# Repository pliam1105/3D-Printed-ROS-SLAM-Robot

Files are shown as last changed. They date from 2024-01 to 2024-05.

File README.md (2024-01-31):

# 3D Printed ROS SLAM Robot
A **3D printed robot** that runs on the **Robot Operating System (ROS 2)** and uses a LiDAR to autonomously navigate around and map a room (**Simultaneous Localization And Mapping**).

https://github.com/pliam1105/3D-Printed-ROS-SLAM-Robot/assets/34167782/ba77c825-f32c-44ad-a219-17dad1da1876

The idea for the project was inspired by James Bruton's [ROS SLAM robot](https://www.youtube.com/watch?v=q1u_cC-5Sac), hence the similarity in some parts of the chassis design and electronics (but everything was designed and built from scratch).

## 3D Printed Chassis

For the chassis I decided to learn about CAD design and 3D printing and make it from scratch. Therefore, I learned how to use **Fusion 360** and designed the required components part-by-part, starting with the motor mounts, next the gears and wheels connected with the drive part, and then connecting them and adding the top platform for the LiDAR and electronics.

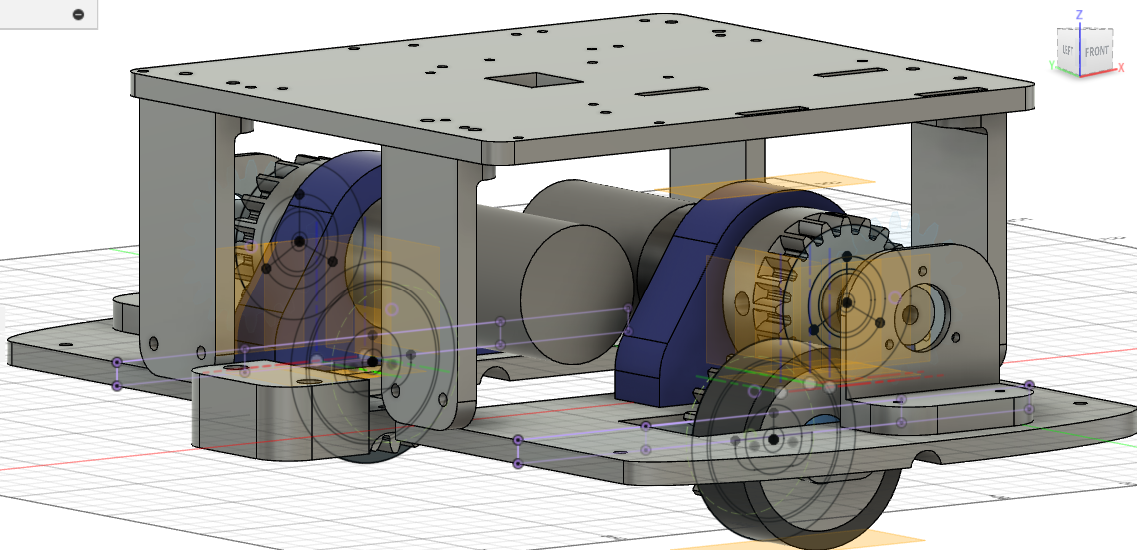
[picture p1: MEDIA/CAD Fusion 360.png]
<table><tr><td align="center"></td></tr><table>

Then I **3D printed** all the parts in my Ender 3 and assembled them with 2 aluminum extrusions, various screws, a rod connecting the wheels, and a couple of ball casters. I also installed all the electronics listed in the next section.

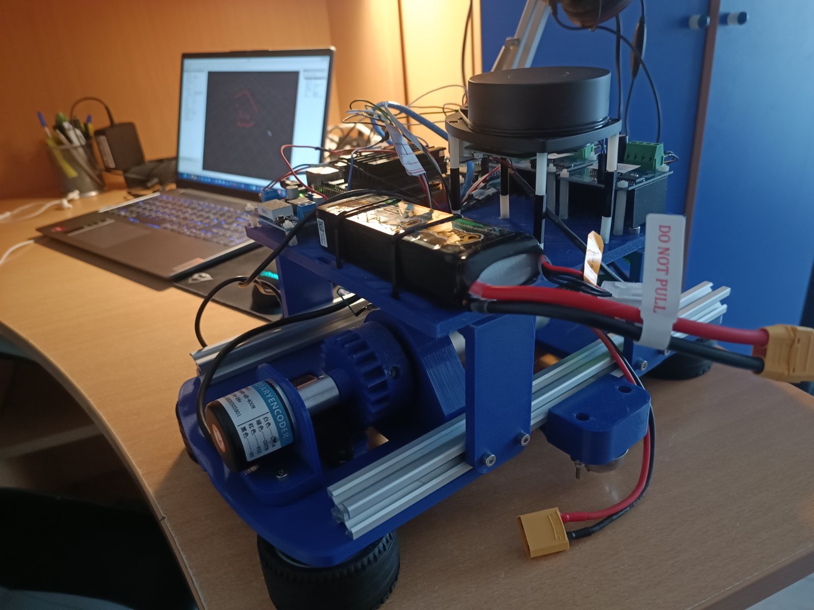
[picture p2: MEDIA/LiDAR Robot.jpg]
<table><tr><td align="center"></td></tr><table>

## Hardware & Connections

The electronics components that I used are the following:

* Two **planetary gear 12V DC motors** (gear ratio $19.2:1$) and two **BTS7960 motor drivers** to control them with the Arduino.
* Two **incremental rotary encoders** for odometry data and controlling the motor speed
* An **RPLiDAR A1** for gathering distance measurements in a $360\degree$ range around the robot
* An **Arduino Mega 2560** to control the motors and record the encoder measurements
* An **NVIDIA Jetson Nano**, working on Ubuntu 20.04 and having ROS 2 Foxy installed, to manage the nodes communicating with the Arduino via Serial for motor control and odometry data transmission

To power the robot, I use:

* A **12V 3S Li-PO battery** that directly powers the motors
* An **LM2596 adjustable step down module**, set to 5V to power the encoders
* A **power bank** (or battery charger) for the Jetson Nano
* The Arduino is powered directly via USB (which also works as Serial) by the Jetson Nano

The connections between the components are depicted in the below Fritzing diagram.

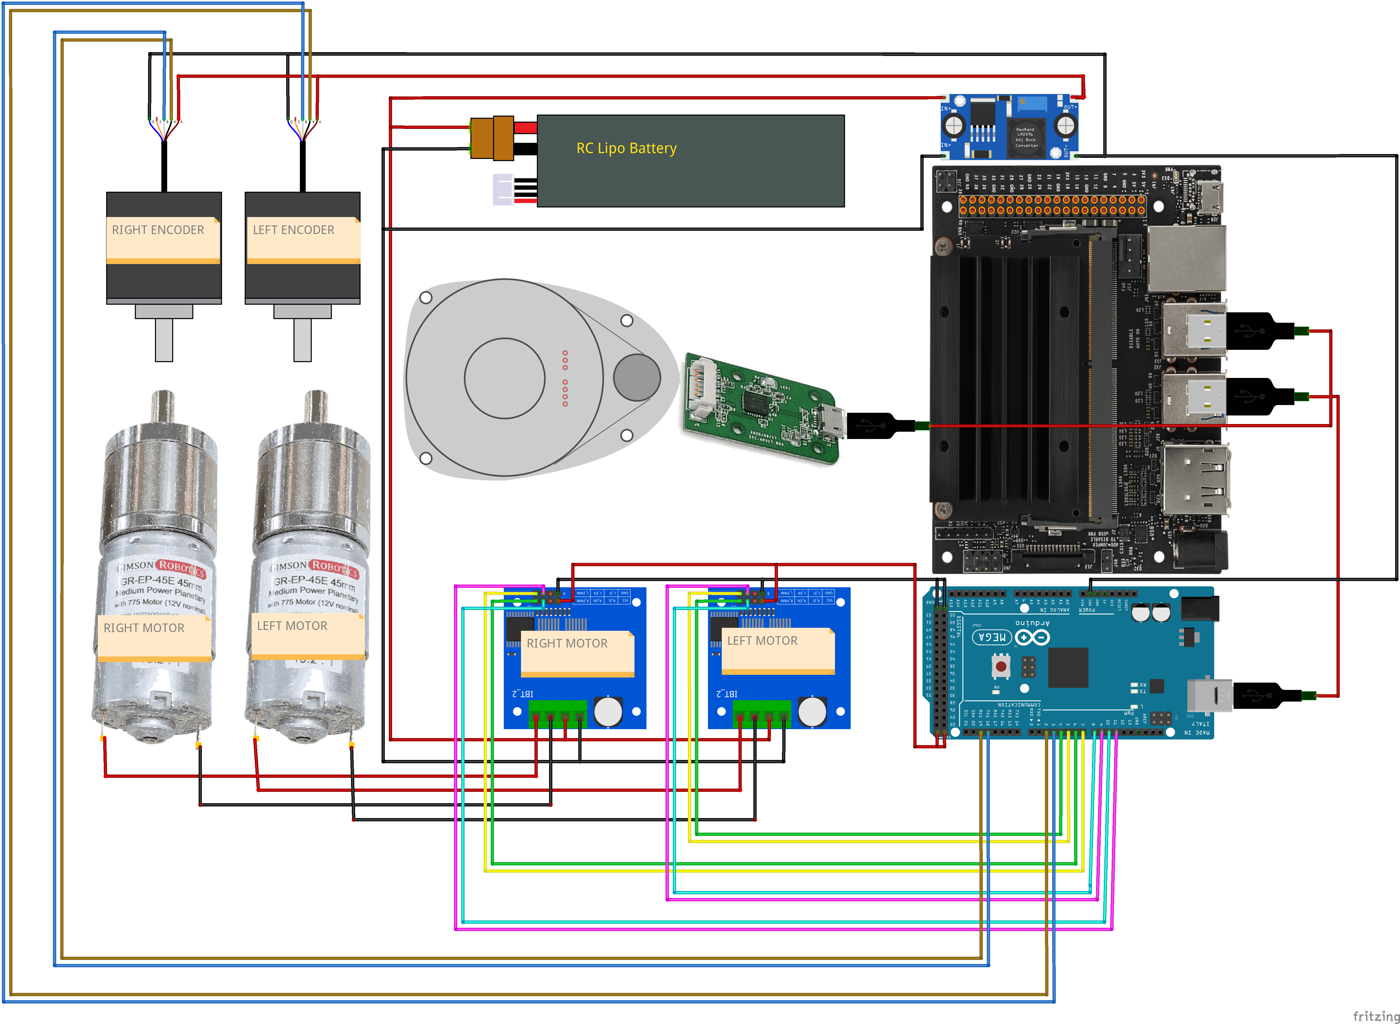
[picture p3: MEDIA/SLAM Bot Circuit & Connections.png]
<table><tr><td align="center"></td></tr><table>

## Arduino Motor Control with PID ([code](Arduino%20Codes/ROSSerial/ROSSerial.ino))

In order to control the motors, I used an Arduino that transfers the velocity commands (given as linear and angular velocity components) from the Jetson Nano and returns the wheels' speeds at any moment.

### Encoder speed calculation and conversion to $m/s$

The first thing needed was to **measure the encoders' rotation speed and direction**. The encoders have two pins, A and B, which give a `HIGH` or `LOW` signal with a phase difference of $90\degree$. Therefore, to measure the speed of rotation we attach an **interrupt** at pin A that triggers when its signal *rises* from `LOW` to `HIGH` (pulse), and count the number of pulses at a certain time interval. To detect the direction we check if the value of B signal is the same as A when we detect a pulse.

Then, to get the speed in terms of $m/s$ (as required by ROS) instead of $pulses/millisecond$ as computed before, I needed to measure the amount of pulses that account to a meter of robot displacement. To do that I put a measuring tape on the ground, moved the robot 1 meter, and noted the number of pulses on the encoders (although later it turned out to not be accurate so I ran the PID controller described below on a certain speed for a specific time and calculated the conversion rate again based on the distance covered).

<table>
    <tr>
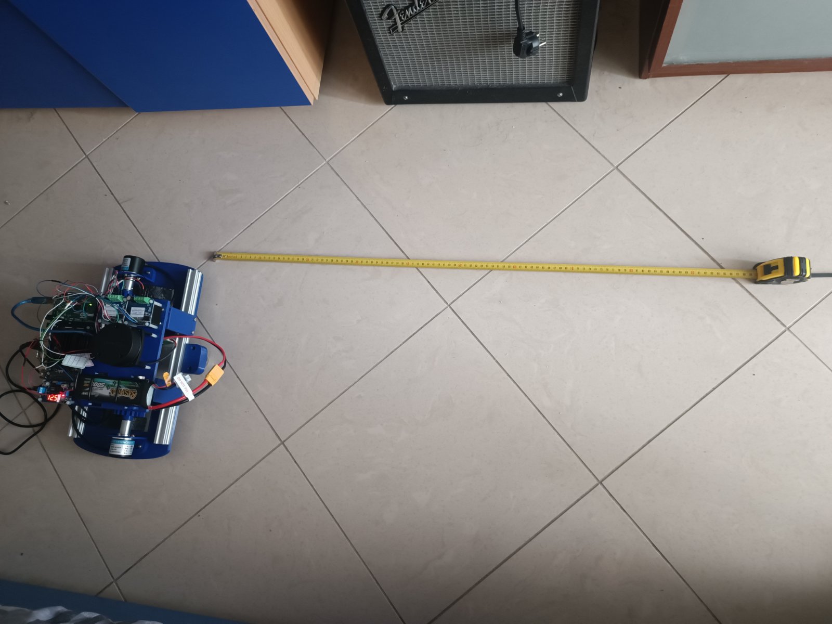
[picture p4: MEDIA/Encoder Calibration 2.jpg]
        <td align="center"></td>
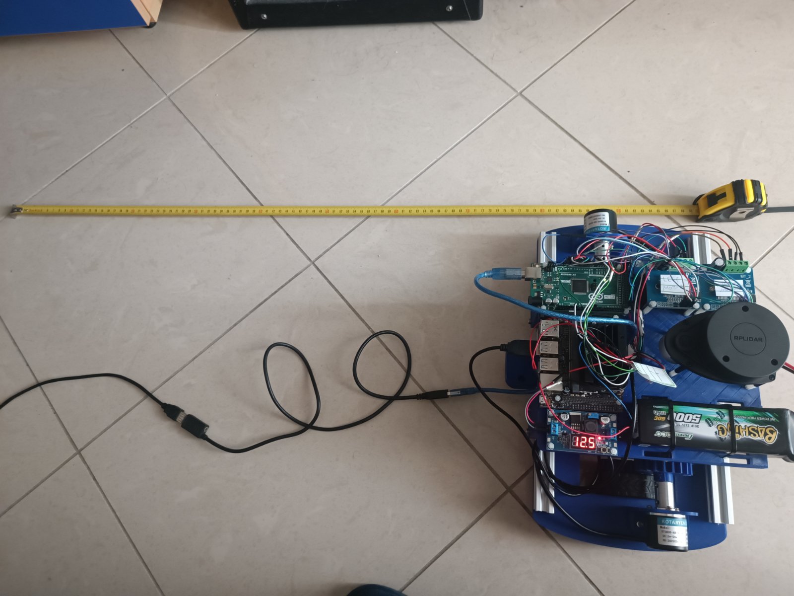
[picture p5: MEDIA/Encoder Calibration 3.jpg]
        <td align="center"></td>
    </tr>
<table>

### PID controller and differential drive

The next, and most important, thing to be implemented is being able to convert the $(linear, angular)$ velocity commands from ROS to **motor speeds**, and **apply them to the motors**, in order to move the robot in the intended way. We first need to convert the 2 given velocity components to the wheel speeds (in $m/s$), that is, implement **differential drive**, which is done using the formulae:

$$
left\ wheel\ speed = linear_X - angular_Z \cdot wheel\ separation / 2
$$

$$
right\ wheel\ speed = linear_X + angular_Z \cdot wheel\ separation / 2
$$

To make the motors move in those specific speeds and mitigate the effects of different motor powers, asymmetrical forces, slippage, and various others, we use a **PID Controller**, which is a *closed loop controller* that gets the encoder measured speeds (*input*) and changes the motors' PWM duty cycle (*output*), using the motor drivers, with the goal of achieving certain speeds. I used the `PID_v1` Arduino library, and tuned the $KP$, $KI$, $KD$ parameters via trial-and-error, finally achieving fast convergence to the intended speed with great accuracy.

## ROS Motor Control Node ([code](ROS%20Codes/arduino_serial/))

Then, I needed to get ROS working with the Arduino and be able to send velocity commands via the `cmd_vel` topic, and receive odometry data via the `odom` one, also publishing the transform `odom` $\rightarrow$ `base_link` (the position and orientation of the robot estimated by the encoder measurements), for which I will explain more in the [SLAM](#slam-node) section.

On the Jetson Nano side, I installed ROS 2 Foxy, working with Ubuntu 20.04, and implemented a package from scratch (`arduino_serial`) that contains the node (with the same name) that will undertake the above functionality.

### Arduino - Jetson Nano Serial Communication

The only feasible way to transmit the required data from/to the Arduino, since the `rosserial` library only works on ROS 1 and `micro-ROS` doesn't work on older Arduino boards, was to use serial communication between Jetson Nano and Arduino. To that end, I used the [`SerialTransfer`](https://github.com/PowerBroker2/SerialTransfer) library and its Python counterpart, [`pySerialTransfer`](https://github.com/PowerBroker2/pySerialTransfer), to send and receive packets of data.

At any moment, I wanted to send velocity commands in the form described [above](#pid-controller-and-differential-drive), but also receive the speed of each wheel, measured by the encoders. That required synchronized data transfer between Jetson Nano and Arduino. When initializing the ROS node and in the Arduino `setup()` function, I made a *handshake* between those two, that is, send a request every 1 second from the Jetson Nano and wait until Arduino responds. Then, at every cycle of the ROS node and the Arduino (which usually have phase difference):
* In the Jetson Nano side, I first send the velocity commands, then wait to receive the encoder speeds from the Arduino
* In the Arduino side, I first wait to receive the velocity commands, then send the encoder speeds

To do that, I needed to send data even when there weren't any new commands or encoder speeds, so I just resent the latest values available.

### Velocity Commands

As mentioned above, the `arduino_serial` node subscribes to the `/cmd_vel` topic to get messages of type `Twist` ,containing $angular\ x,y,z$ and $linear\ x,y,z$ components, from which we only care about the $linear_x$ and $angular_z$ ones, which it then forwards to the Arduino. I tested that functionality using the `teleop_twist_keyboard` package and the respective node.

### Odometry feedback and pose estimation

The navigation nodes used in the [next section](#simultaneous-localization-and-mapping-code) require the publishing of `Odometry` messages, containing the estimated pose and velocity of the robot, as well as the transform `odom` $\rightarrow$ `base_link`, that is, the estimated pose frame (`base_link`) with respect to a fixed frame (`odom`).

I compute the $(linear, angular)$ velocity components using the following formulae:

$$
linear_x = (left\ wheel\ speed + right\ wheel\ speed) / 2
$$

$$
angular_z = \frac{right\ wheel\ speed - left\ wheel\ speed}{wheel\ separation}
$$

I also time-integrate the wheel speeds to get the pose estimation using the following formulae (applied at each time-step with new encoder data):

$$
\text{Angle displacement:}\ d\theta = angular_z \cdot dt
$$

$$
\text{Distance left wheel traveled:}\ d_{left} = left\ wheel\ speed \cdot dt
$$

$$
\text{Distance right wheel traveled:}\ d_{right} = right\ wheel\ speed \cdot dt
$$

$$
\text{Distance point of reference (center) traveled:}\ d_{center} = (d_{left} + d_{right})/2
$$

$$
\text{$x$ displacement:}\ d_x = d_{center} \cdot \cos{(\theta + d\theta/2)}
$$

$$
\text{$y$ displacement:}\ d_y = d_{center} \cdot \sin{(\theta + d\theta/2)}
$$

$$
\text{New $x$ coordinate:}\ x' = x + dx
$$

$$
\text{New $y$ coordinate:}\ y' = y + dy
$$

$$
\text{New $\theta$ orientation:}\ \theta' = \theta + d\theta
$$

I tested the odometry pose estimation by moving the robot around with `teleop_twist_keyboard` around the room and checking the drift of LiDAR data with respect to a fixed coordinate frame (`odom`), by visualizing it with RViz 2.

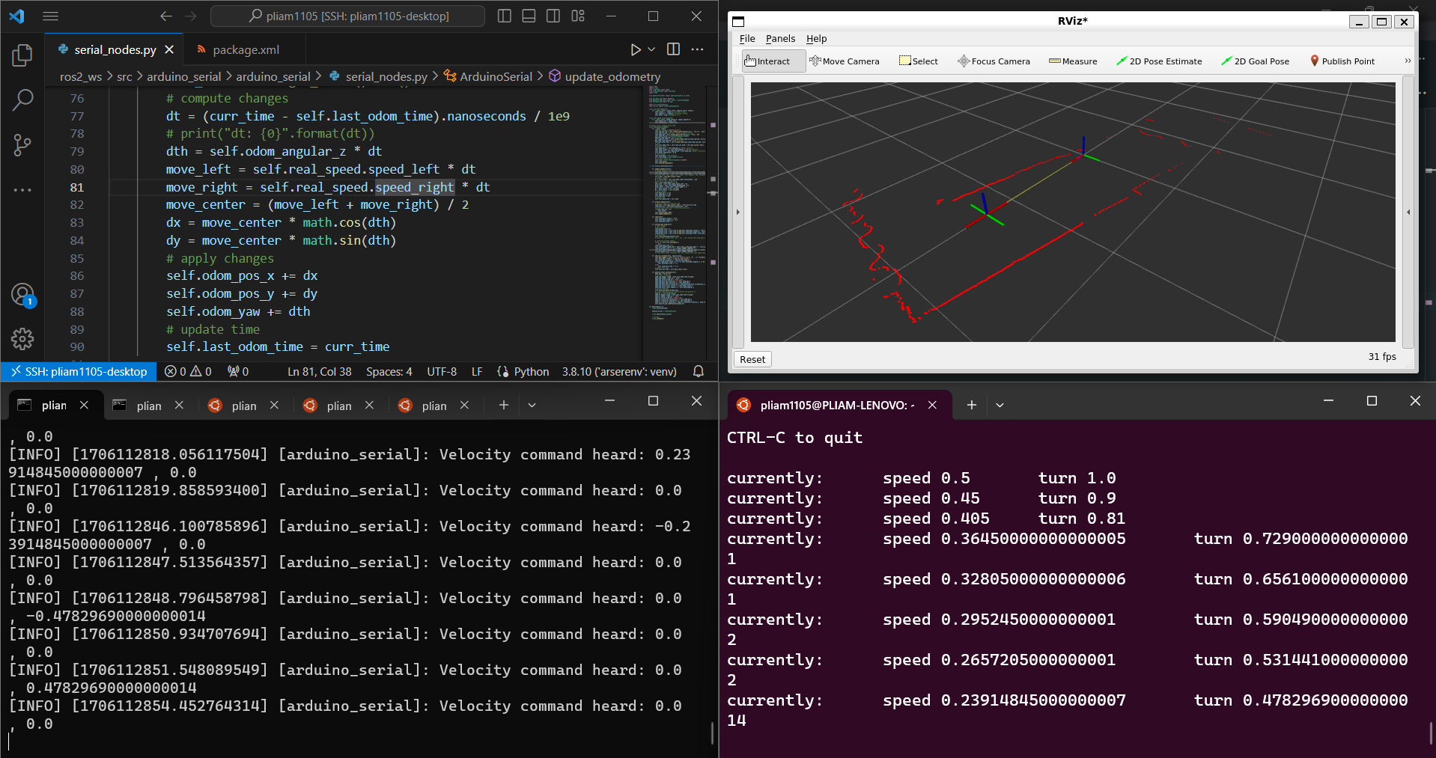
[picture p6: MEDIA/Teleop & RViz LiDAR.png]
<table><tr><td align="center"></td></tr><table><br>

## Simultaneous Localization and Mapping ([code](ROS%20Codes/slam_bot/))

The next step, after being able to control the robot's velocity and get a pose estimation based on its encoders, is to incorporate LiDAR data and implement **Simultaneous Localization and Mapping (SLAM)**, and also **navigate** around the room autonomously.

### LiDAR Node

To convert the LiDAR data, which are transmitted via USB to the Jetson Nano, to a ROS-compatible format (`LaserScan` messages), I used the [RPLiDAR ROS](https://github.com/allenh1/rplidar_ros) library, which launches a node that publishes to the `/scan` topic, which I could visualize in RViz 2 as shown below.

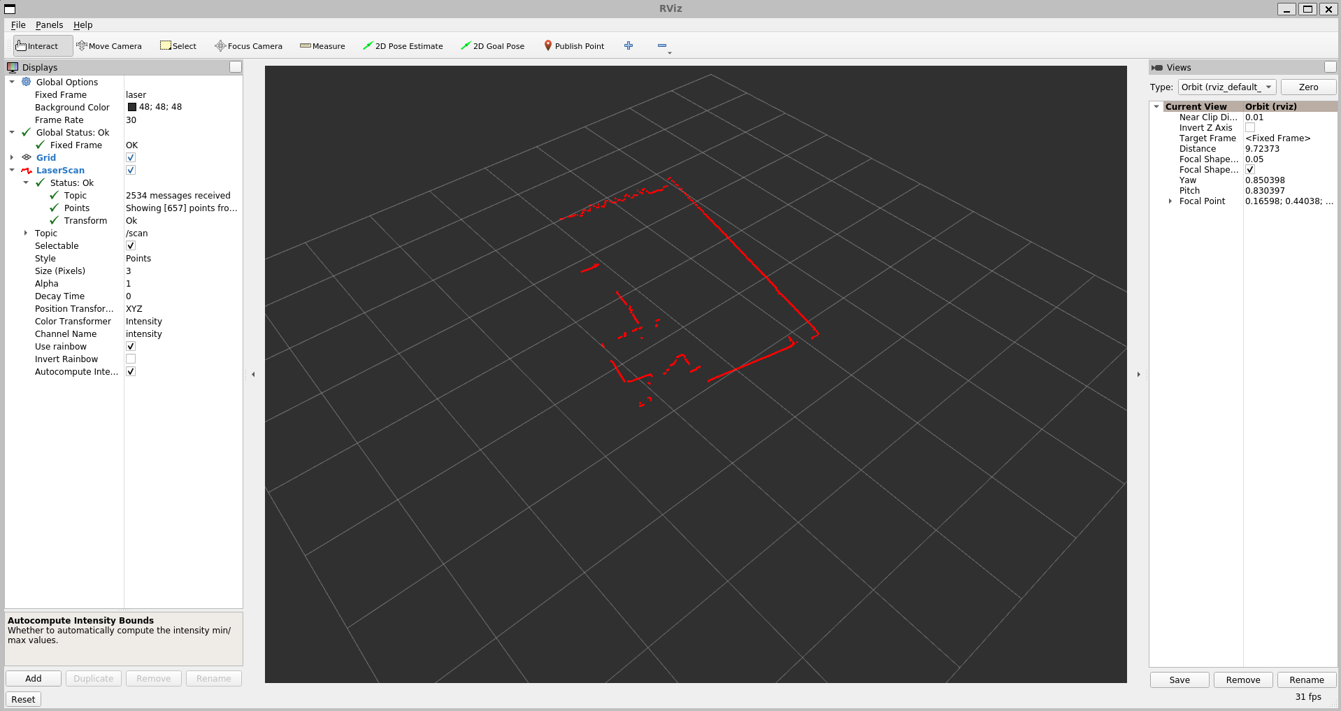
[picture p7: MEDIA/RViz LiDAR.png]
<table><tr><td align="center"></td></tr><table><br>

### Robot & Joint State Publishers

ROS coordinates are based on certain *frames*, that is coordinate frames that are related with each other using *transforms* (which can be published and computed using `tf2`), that are all part of the *TF tree*. In terms of the robot, these frames are described using *links*, which are connected with each other via child-parent relationships and defined using translations.

Therefore, a robot is described by defining all these links and relations in a URDF file (an XML file). This description is published in the TF tree using a *Robot State Publisher* (using the `robot_state_publisher` package and respective node).

Also, since there are joints with variable orientation (or other types of movement), their states are published using a *Joint State Publisher* (using the `joint_state_publisher` package and node and their GUI counterparts that enable changing the states using sliders).

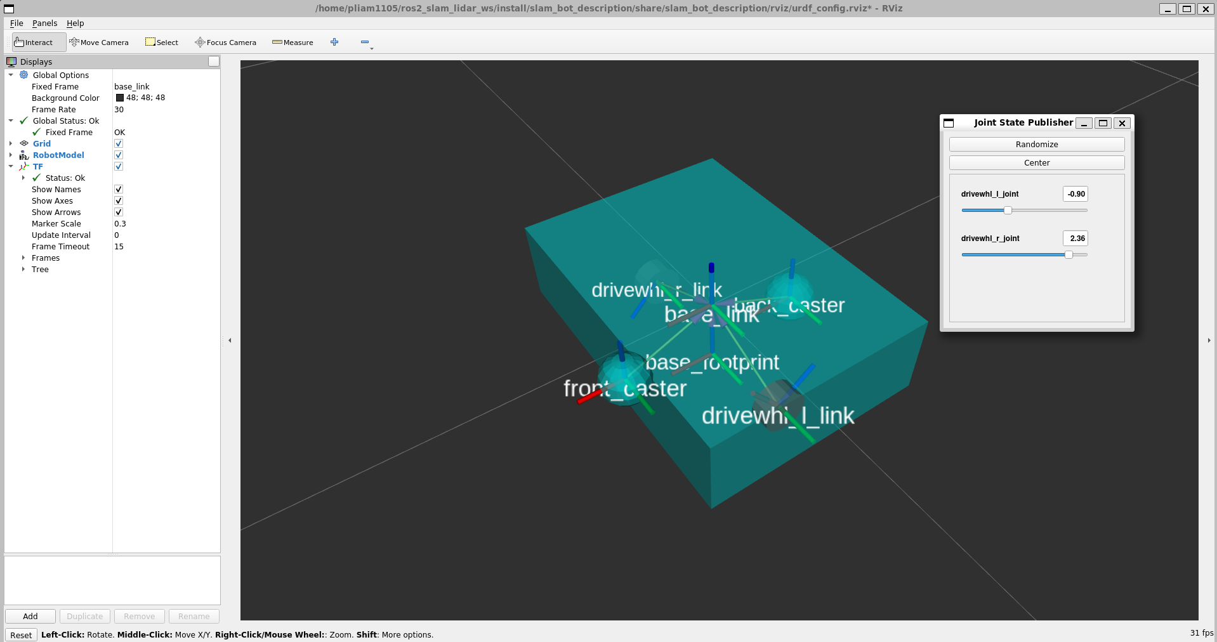
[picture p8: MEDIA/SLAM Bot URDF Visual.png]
<table><tr><td align="center"></td></tr><table><br>

### SLAM Node

This is the point where all the above aspects start connecting with each other. The fundamental part of an autonomous robot is being able to **map an unknown area and localize itself in it**; this is the essence of **SLAM**. To implement that functionality, I used the `slam_toolbox` package, specifically the `async_slam_toolbox_node` node, which receives the odometry and sensory data published and creates a map, which it aligns with the robot's coordinate frame to predict a more accurate location estimation.

That's where the coordinate transforms mentioned in the [Motor Control Node](#ros-motor-control-node-code) section come handy. The core frames used in localization and mapping using ROS are: `map`, `odom`, and `base_link` (and `base_laser` or `laser` representing LiDAR, but this is usually computed with respect to `base_link`).

* `map` is the frame that represented the real-world environment of the robot, which is supposed to be stationary
* `odom` is the frame that stays fixed with respect to the starting position of the robot, and is used to depict the robot's odometry location estimate
* `base_link` is the frame that represents the robot's position

The `odom` $\rightarrow$ `base_link` transform is computed as described in the [odometry](#odometry-feedback-and-pose-estimation) section, using the encoder data.

The `map` $\rightarrow$ `odom` transform is computed by the localization node, in this case one from the `slam_toolbox` package, and its purpose is to align the robot's estimate of its position with the map of its environment using its sensory data.

The result of that functionality is visualized as shown below, in RViz 2.

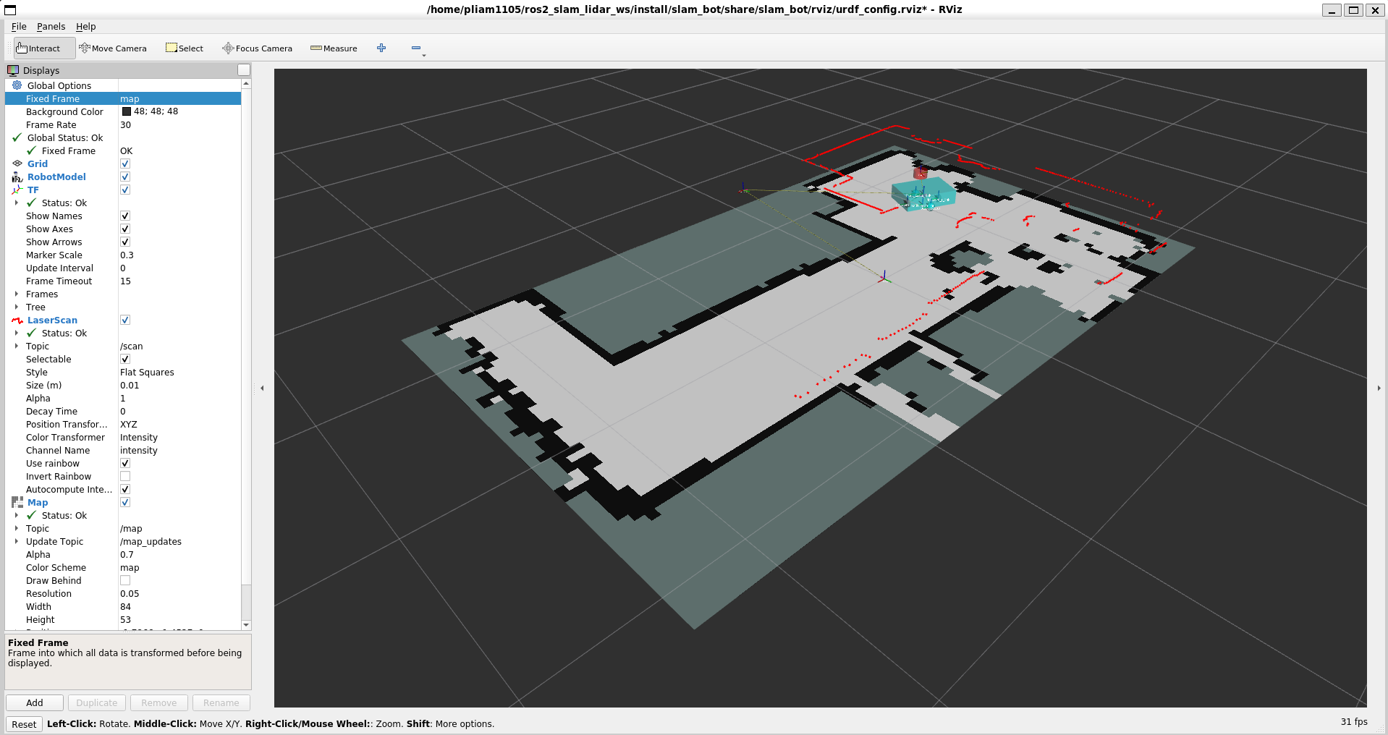
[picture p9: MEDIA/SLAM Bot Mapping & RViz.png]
<table><tr><td align="center"></td></tr><table><br>

### Navigation Nodes

After locating itself in the environment, the robot's purpose is to complete tasks in it, and this involves moving to specific locations on its own. This is the navigation part of the project, which is implemented using the `navigation2` package (and the `nav2_bringup` to launch all the required nodes at once).

It takes the map computed from `slam_toolbox` and creates a *costmap* based on it, that is, a map representing the ability to traverse each part of the map, with relation to the occupied areas (which are also *inflated* by a radius, accounting for the robot's size).

Then, a *planner* takes that costmap and the end goal given by the user (via RViz or a service call), and computes, for some time ahead, the optimal path to achieve that goal. This updates at specific intervals, taking into account the new state of the robot and updated map.

Finally, a *controller* takes the path computed by the planner and publishes the velocity commands to follow it, which then the Arduino receives and applies motor speeds accordingly. The controller also updates at specific intervals, integrating the newest path and robot state received.

There are also some *backup nodes* that are activated in certain instances to recover the robot's location and find a new way to accomplish the goal (all this structure works using decision trees).

A visualization of the state of the robot, the map, and the path computed in a certain instance, in RViz 2 is provided below.

<table><tr><td align="center"><img src="MEDIA/SLAM Bot Navigation RViz.jpg" width=75%"></td></tr><table><br>

## Final Result

The final result is a robot that is able to **receive end goal commands and navigate to them on its own**, able to adapt to unknown environments and unexpected instances effectively. A snippet of the robot working in real life is given below.

<table><tr><td align="center"></td></tr><table><br>

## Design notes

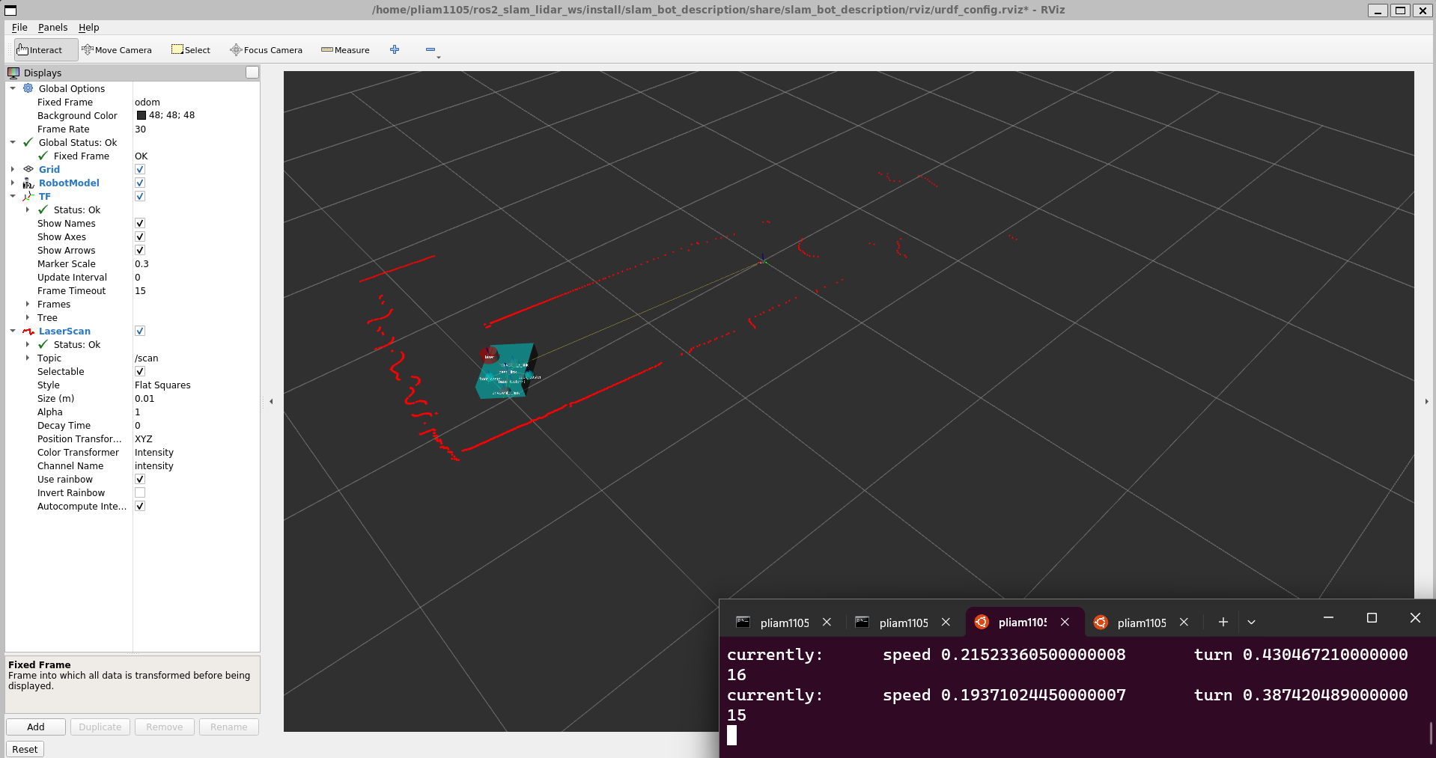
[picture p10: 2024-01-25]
MEDIA/Teleop LiDAR & Odom RViz URDF.png

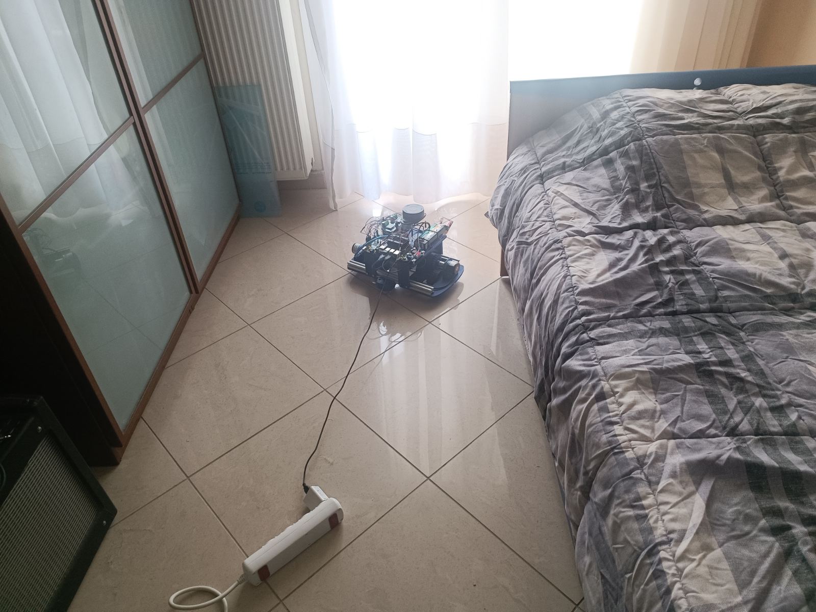
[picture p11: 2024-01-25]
MEDIA/LiDAR URDF Odom RViz Room Image.jpg

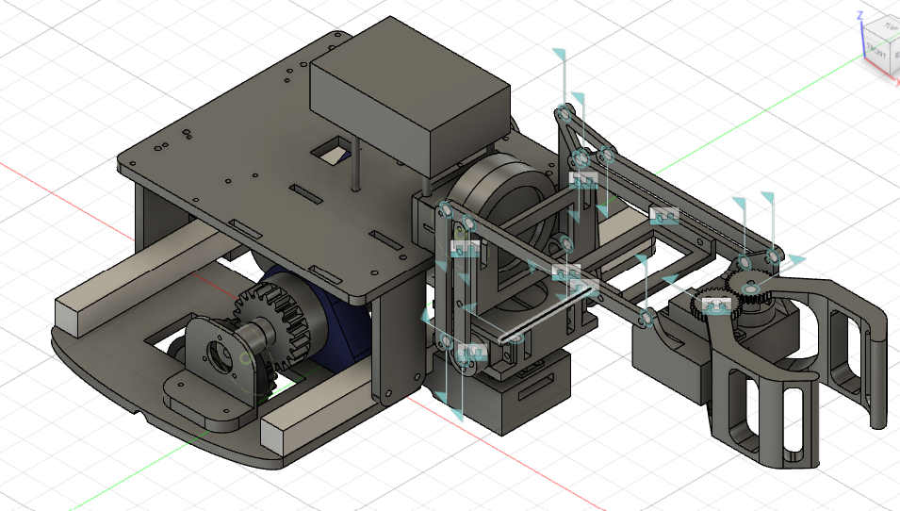
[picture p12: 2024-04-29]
MEDIA/SLAM Bot CAD with Robotic Arm and Camera.png

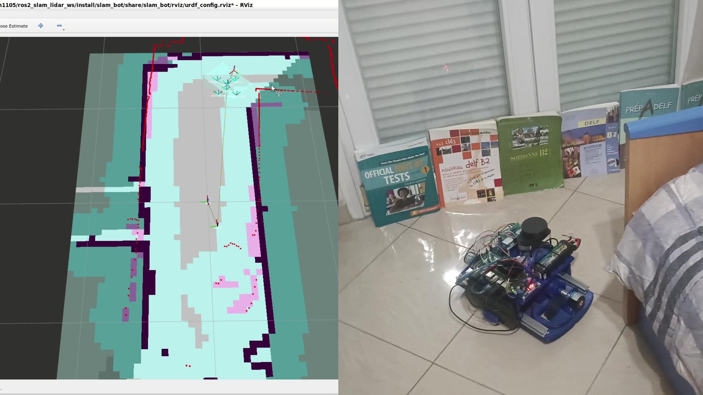
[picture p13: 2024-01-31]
MEDIA/SLAM Navigation RViz & Camera Image.jpg

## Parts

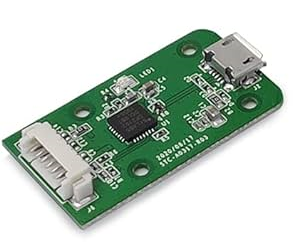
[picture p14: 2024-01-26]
Fritzing Connections/Parts/RPLiDAR USB Connector.png

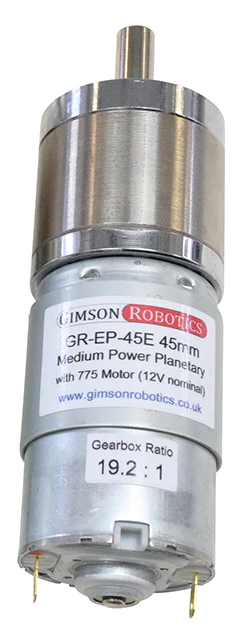
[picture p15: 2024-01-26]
Fritzing Connections/Parts/Planetary Gearmotor.png

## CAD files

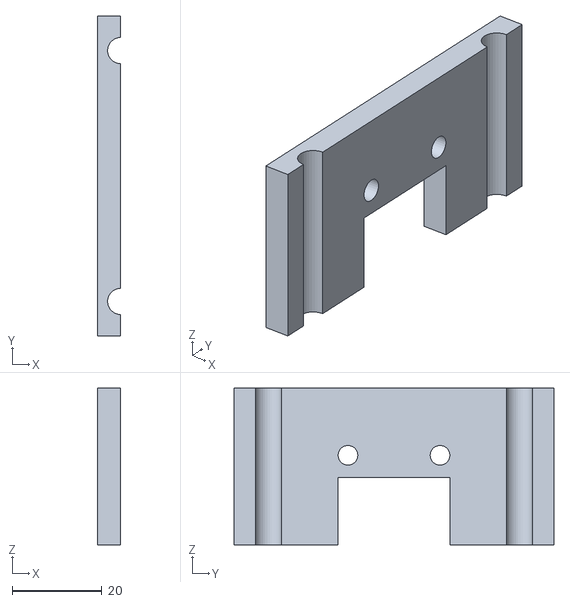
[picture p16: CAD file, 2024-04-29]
3D PRINT/STL/Camera Mount/SpacerMountBack.stl
5.22 x 71.5 x 35.0

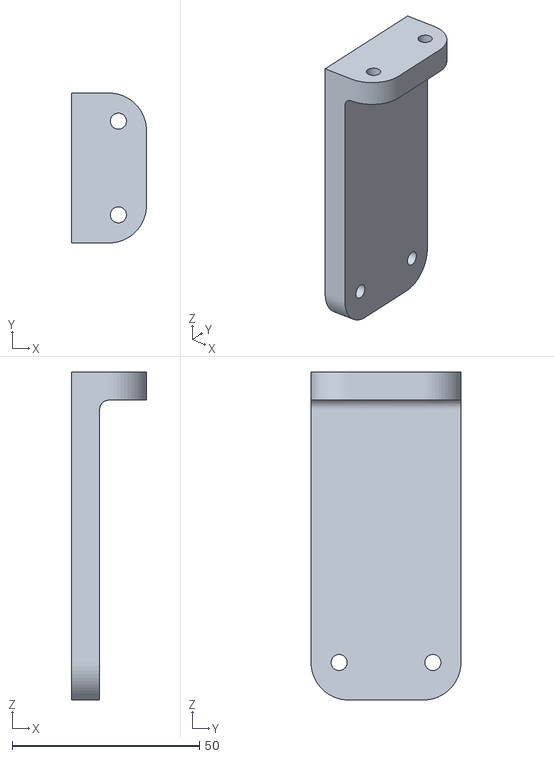
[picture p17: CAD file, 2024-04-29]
3D PRINT/STL/Connector.stl
20.0 x 40.0 x 87.5

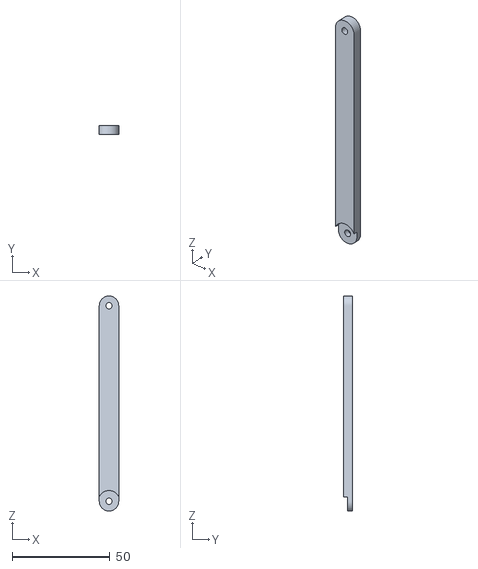
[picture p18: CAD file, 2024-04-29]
3D PRINT/STL/Robotic Arm/RightParallelLink.stl
10.0 x 4.50 x 110.0

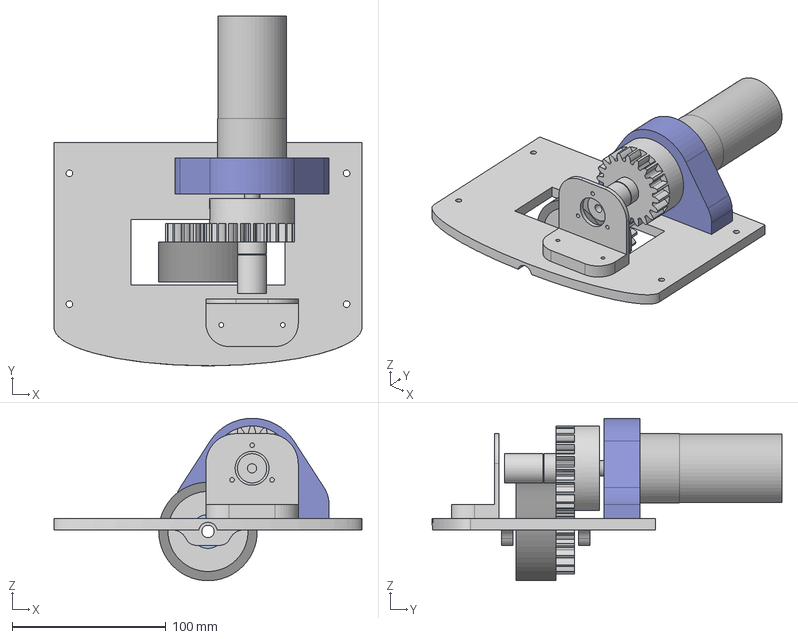
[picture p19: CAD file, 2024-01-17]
Fusion360/Drive.step
200.0 x 227.0 x 105.5 mm
Spur Gear (20 teeth)
Motor
Spur Gear (20 teeth) (1)

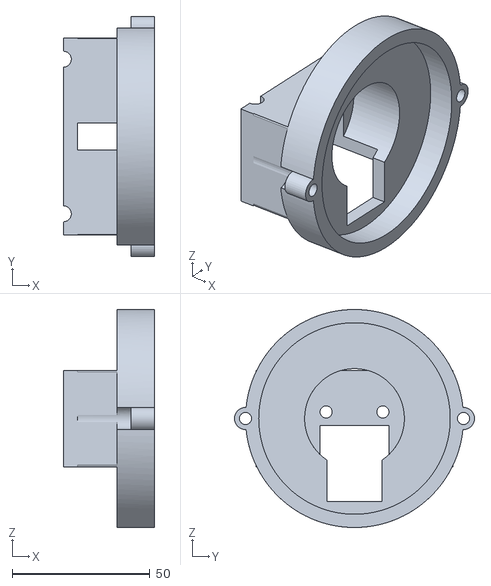
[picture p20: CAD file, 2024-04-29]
3D PRINT/STL/Camera Mount/Bridge.stl
33.1 x 87.0 x 79.0

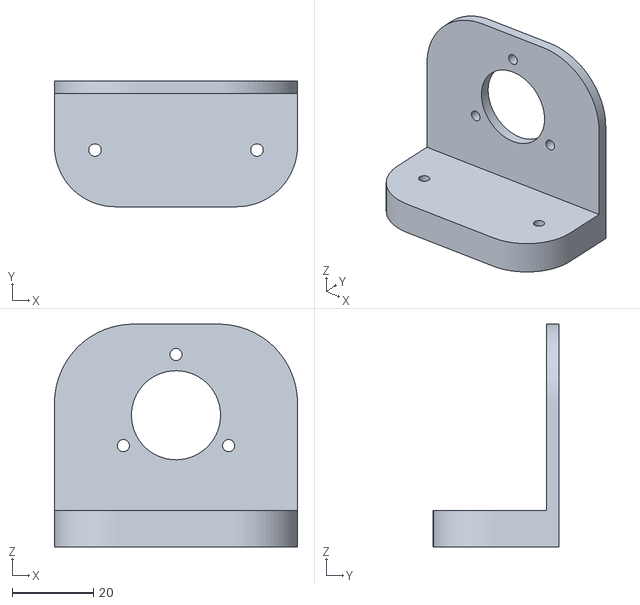
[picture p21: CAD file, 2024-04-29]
3D PRINT/STL/EncoderMount.stl
60.0 x 31.0 x 55.0

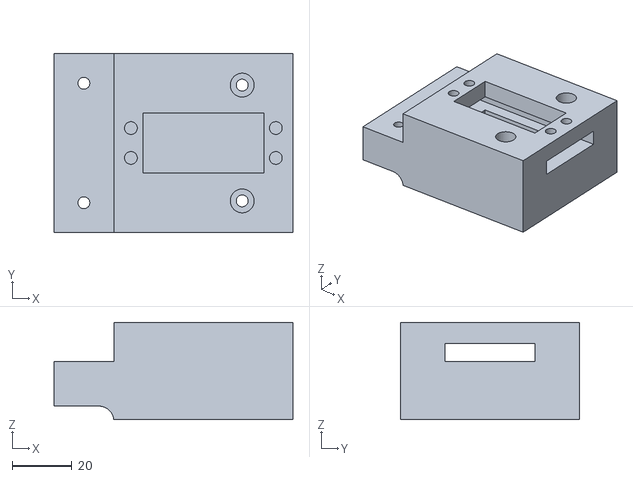
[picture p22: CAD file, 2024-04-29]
3D PRINT/STL/Robotic Arm/ArmMountCase.stl
80.0 x 60.0 x 32.5

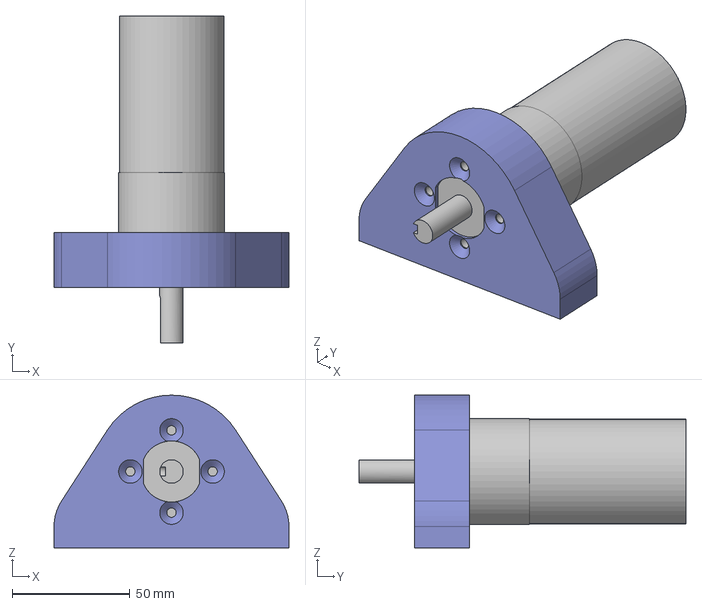
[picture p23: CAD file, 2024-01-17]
Fusion360/Motor.step
100.0 x 139.0 x 65.0 mm

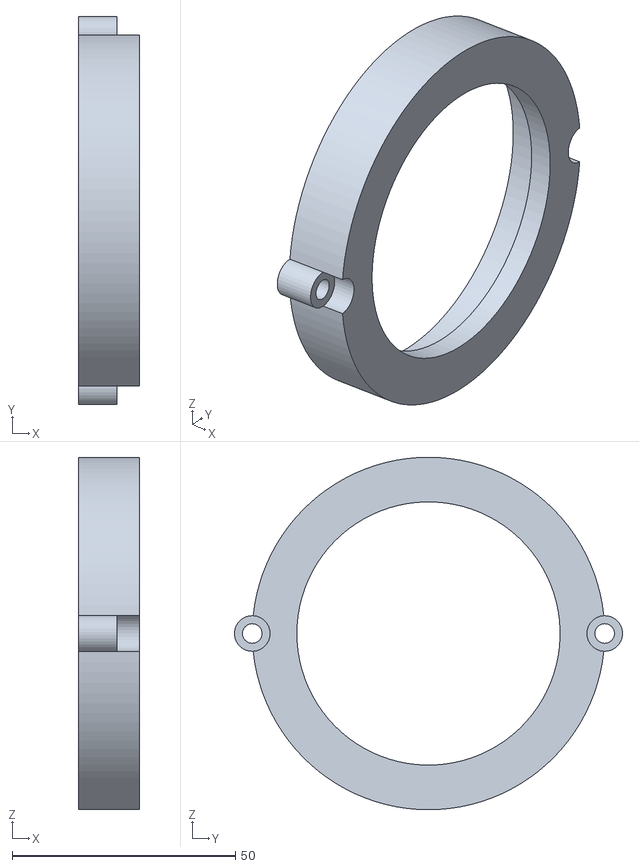
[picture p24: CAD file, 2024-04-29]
3D PRINT/STL/Camera Mount/CameraMountFront.stl
13.6 x 87.0 x 79.0

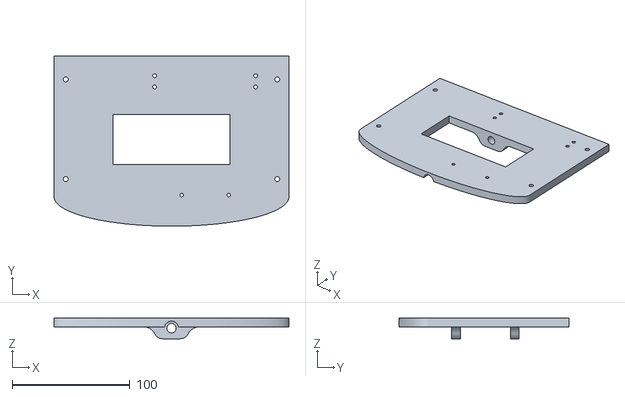
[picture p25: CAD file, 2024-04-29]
3D PRINT/STL/Chassis.stl
200.0 x 145.0 x 17.5

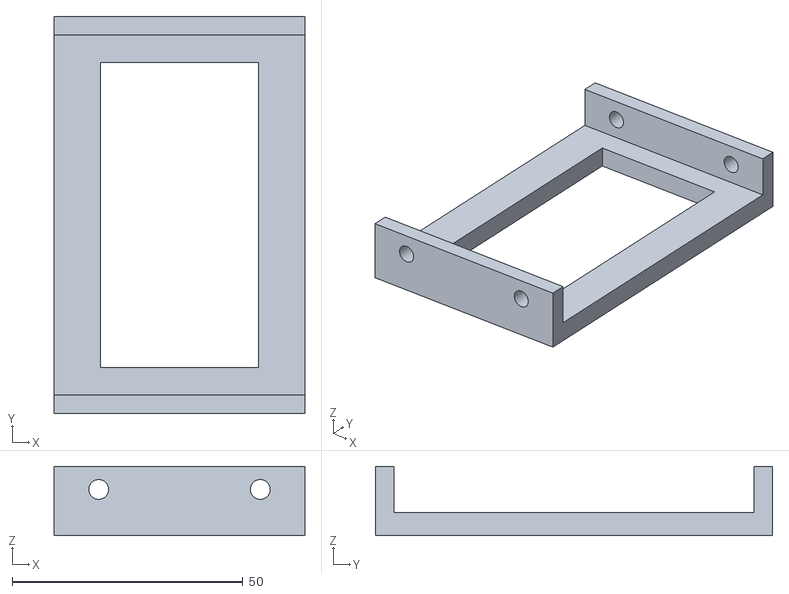
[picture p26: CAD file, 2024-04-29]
3D PRINT/STL/Robotic Arm/SecondSupport.stl
54.3 x 86.0 x 15.0

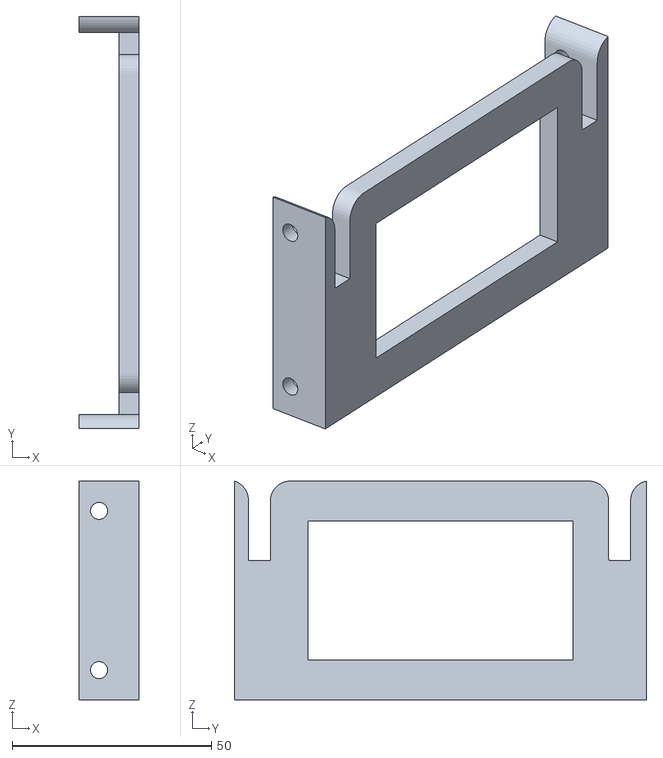
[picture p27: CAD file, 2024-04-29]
3D PRINT/STL/Robotic Arm/FirstSupport.stl
15.0 x 103.5 x 55.0

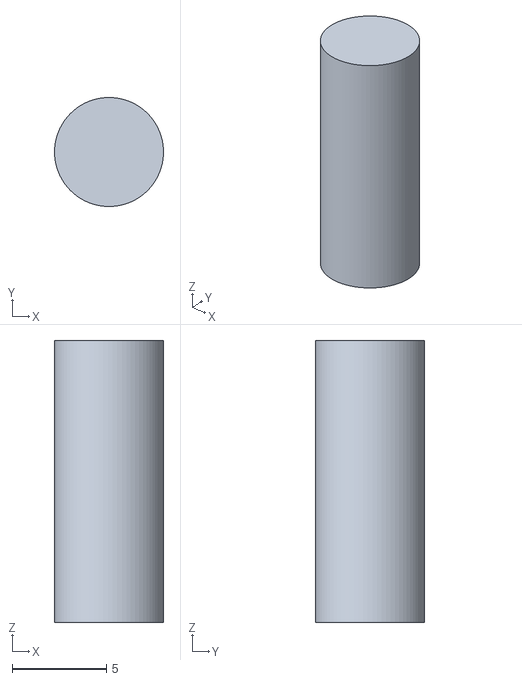
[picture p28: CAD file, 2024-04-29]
3D PRINT/STL/ShaftEncoder.stl
5.80 x 5.80 x 15.0

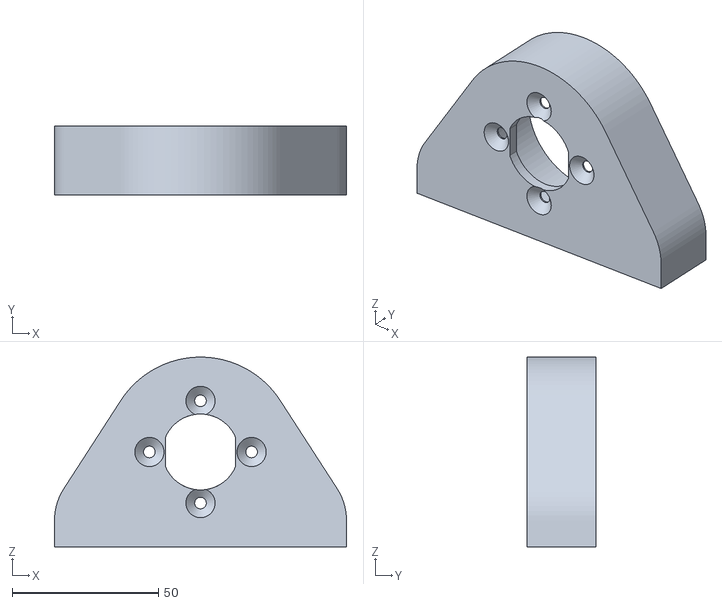
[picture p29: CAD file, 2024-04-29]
3D PRINT/STL/MotorMount.stl
100.0 x 23.5 x 65.0

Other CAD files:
3D PRINT/STL/Robotic Arm/LeftMotionLink.stl
3D PRINT/STL/CasterWheelMount.stl
3D PRINT/STL/Robotic Arm/RightDriveLink.stl
3D PRINT/STL/Gear.stl
3D PRINT/STL/Plate.stl
3D PRINT/STL/Robotic Arm/DriveGripper.stl
3D PRINT/STL/Robotic Arm/DrivenGripper.stl
3D PRINT/STL/Robotic Arm/GripperCase.stl
3D PRINT/STL/Robotic Arm/GripperSpacerReplacement.stl
3D PRINT/STL/Robotic Arm/LeftDriveLink.stl
3D PRINT/STL/Robotic Arm/LeftLongLink.stl
3D PRINT/STL/Robotic Arm/LeftSupportLink.stl
3D PRINT/STL/Robotic Arm/RightDownLink.stl
3D PRINT/STL/Robotic Arm/RightTriangle.stl
3D PRINT/STL/Robotic Arm/RightUpLink.stl
3D PRINT/STL/Robotic Arm/VerticalMountCase.stl
3D PRINT/STL/Wheel.stl

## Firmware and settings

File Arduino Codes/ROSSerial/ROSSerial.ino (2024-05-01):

#include <Servo.h>
#include <PID_v1.h>
#include "SerialTransfer.h"

//servos
#define servo1 22
#define servo2 23
#define servo3 24
#define servo4 25

//left motor
#define leftRPWM 4
#define leftLPWM 5
#define leftENR 8
#define leftENL 9

//right motor
#define rightRPWM 6
#define rightLPWM 7
#define rightENR 10
#define rightENL 11

//left encoder
#define leftA 2
#define leftB 3

//right encoder
#define rightA 19
#define rightB 18

//servo variables
Servo Servo1, Servo2, Servo3, Servo4;

const float valueRange1[] = {30, 80};
const float angleRange1[] = {-20, 30};

const float valueRange2[] = {40, 110};
const float angleRange2[] = {10, 80};

const float valueRange3[] = {90, 160};
const float angleRange3[] = {-50, 20};
const float angleConstrain3[] = {50, 120}; //wrt the previous link, this is where angle3 lies

const float valueRange4[] = {50, 0};
const float angleRange4[] = {25, 75};

const double metersToPulses = 1670.0; //for meter -> pulses conversion
// const double wheelDistance = 0.25; //for angular velocity computation

//encoder variables
volatile long leftCounter = 0, rightCounter = 0;
const long encoderInterval = 10;
unsigned long lastTime, currentTime, startTime;
volatile bool changeLeft = false, changeRight = false;
double leftEncoderSpeed, rightEncoderSpeed;//measured speeds

//PID variables
const double KP = 1, KI = 1.5, KD = 0.05;
double leftMotorSpeed, rightMotorSpeed;
double leftOutput, rightOutput;
double leftPWM, rightPWM;

//ROS Twist linear and angular components
// double linearX, angularZ;
int stop = 1;

PID leftSpeedPID(&leftEncoderSpeed, &leftOutput, &leftMotorSpeed, KP, KI, KD, DIRECT);
PID rightSpeedPID(&rightEncoderSpeed, &rightOutput, &rightMotorSpeed, KP, KI, KD, DIRECT);

//Serial communication
SerialTransfer ros_transfer;

struct __attribute__((packed)) data_struct{
  float vel_left, vel_right;
  int32_t stop;
  float angle1, angle2, angle3, angle4;
};

uint16_t packet_size = 0;

void setup() {
  //initialize servos
  float initialAngles[4] = {0, 10, 50, 25};
  moveServos(initialAngles[0], initialAngles[1], initialAngles[2], initialAngles[3]);

  //attach servos
  Servo1.attach(servo1);
  Servo2.attach(servo2);
  Servo3.attach(servo3);
  Servo4.attach(servo4);

  //define motor pin modes
  pinMode(leftRPWM, OUTPUT);
  pinMode(leftLPWM, OUTPUT);
  pinMode(rightRPWM, OUTPUT);
  pinMode(rightLPWM, OUTPUT);
  pinMode(leftENR, OUTPUT);
  pinMode(leftENL, OUTPUT);
  pinMode(rightENR, OUTPUT);
  pinMode(rightENL, OUTPUT);

  //enable motor movement in both directions
  digitalWrite(leftENL, HIGH);
  digitalWrite(leftENR, HIGH);
  digitalWrite(rightENL, HIGH);
  digitalWrite(rightENR, HIGH);

  //Serial communication
  Serial.begin(115200);
  ros_transfer.begin(Serial);

  //set encoder pin modes
  pinMode(leftA, INPUT_PULLUP);
  pinMode(leftB, INPUT_PULLUP);
  pinMode(rightA, INPUT_PULLUP);
  pinMode(rightB, INPUT_PULLUP);

  attachInterrupt(0, changeLeftA, RISING);
  attachInterrupt(4, changeRightA, RISING);

  lastTime = startTime = millis();

  //PID setup
  leftSpeedPID.SetOutputLimits(-100, 100);
  rightSpeedPID.SetOutputLimits(-100, 100);
  leftSpeedPID.SetSampleTime(10);
  rightSpeedPID.SetSampleTime(10);
  leftSpeedPID.SetMode(AUTOMATIC);
  rightSpeedPID.SetMode(AUTOMATIC);

  //wait for handshake call
  while(true){
    if(ros_transfer.available()){
      packet_size = 0;
      int32_t ok;
      packet_size = ros_transfer.rxObj(ok, packet_size);//should be 100
      if(ok == 100){
        //send response
        packet_size = 0;
        packet_size = ros_transfer.txObj((int32_t)200, packet_size);
        ros_transfer.sendData(packet_size);
        break;
      }
    }
  }
}

void loop() {
  //receiving commands
  if(ros_transfer.available()){
    packet_size = 0;
    data_struct new_cmd = data_struct();
    packet_size = ros_transfer.rxObj(new_cmd, packet_size);

    //take action
    stop = new_cmd.stop;
    // linearX = new_cmd.linear_x;
    // angularZ = new_cmd.angular_z;
    leftMotorSpeed = new_cmd.vel_left;
    rightMotorSpeed = new_cmd.vel_right;

    data_struct real_data = new_cmd;//to copy & constrain servo values
    moveServos(real_data.angle1, real_data.angle2, real_data.angle3, real_data.angle4);

    //send encoder speeds
    real_data.vel_left = leftEncoderSpeed;
    real_data.vel_right = rightEncoderSpeed;

    packet_size = 0;
    packet_size = ros_transfer.txObj(real_data, packet_size);
    ros_transfer.sendData(packet_size);
  }

  //compute encoder speeds
  currentTime = millis();
  if(currentTime - lastTime >= encoderInterval){
    //compute speeds in pulses/millisecond
    leftEncoderSpeed = ((double)leftCounter)/((double)currentTime - lastTime);
    rightEncoderSpeed = ((double)rightCounter)/((double)currentTime - lastTime);
    //convert to meters/second
    leftEncoderSpeed = leftEncoderSpeed * 1000.0 / metersToPulses;
    rightEncoderSpeed = rightEncoderSpeed * 1000.0 / metersToPulses;
    leftCounter = rightCounter = 0;
    lastTime += encoderInterval;
  }
  
  //compute wheel velocities from linear and angular velocity components
  // leftMotorSpeed = linearX - angularZ * wheelDistance / 2.0;
  // rightMotorSpeed = linearX + angularZ * wheelDistance / 2.0;
  //apply PID
  leftSpeedPID.Compute();
  rightSpeedPID.Compute();
  leftPWM += leftOutput;
  rightPWM += rightOutput;
  // Serial.print(leftPWM);
  // Serial.print(", ");
  // Serial.println(rightPWM);
  if(leftPWM >=0){
    analogWrite(leftRPWM, leftPWM);
    analogWrite(leftLPWM, 0);
  }else{
    analogWrite(leftRPWM, 0);
    analogWrite(leftLPWM, -leftPWM);
  }
  if(rightPWM >=0){
    analogWrite(rightRPWM, rightPWM);
    analogWrite(rightLPWM, 0);
  }else{
    analogWrite(rightRPWM, 0);
    analogWrite(rightLPWM, -rightPWM);
  }

  if(stop != 1){
    // if(leftSpeedPID.GetMode() == MANUAL) leftSpeedPID.SetMode(AUTOMATIC);
    // if(rightSpeedPID.GetMode() == MANUAL) rightSpeedPID.SetMode(AUTOMATIC);
    digitalWrite(leftENL, HIGH);
    digitalWrite(leftENR, HIGH);
    digitalWrite(rightENL, HIGH);
    digitalWrite(rightENR, HIGH);
  }else{
    // leftSpeedPID.SetMode(MANUAL);
    // rightSpeedPID.SetMode(MANUAL);
    analogWrite(leftLPWM, 0);
    analogWrite(leftRPWM, 0);
    analogWrite(rightLPWM, 0);
    analogWrite(rightRPWM, 0);
    digitalWrite(leftENL, LOW);
    digitalWrite(leftENR, LOW);
    digitalWrite(rightENL, LOW);
    digitalWrite(rightENR, LOW);
    leftPWM = rightPWM = 0;
  }
}

void changeLeftA(){
  if(digitalRead(leftA)!=digitalRead(leftB)){
    //clockwise but reversed -> forward is +
    leftCounter--;
  }else{
    //counterclockwise but reversed
    leftCounter++;
  }
  changeLeft = true;
}

void changeRightA(){
  if(digitalRead(rightA)!=digitalRead(rightB)){
    //clockwise
    rightCounter++;
  }else{
    //counterclockwise
    rightCounter--;
  }
  changeRight = true;
}

void moveServos(float &angle1, float &angle2, float &angle3, float &angle4){
  //constraint angles
  angle1 = constrain(angle1, angleRange1[0], angleRange1[1]);
  angle2 = constrain(angle2, angleRange2[0], angleRange2[1]);
  angle3 = constrain(angle3, angleConstrain3[0], angleConstrain3[1]);
  angle4 = constrain(angle4, angleRange4[0], angleRange4[1]);

  //calculate values from angles with map
  float values[4];
  values[0] = map(angle1, angleRange1[0], angleRange1[1], valueRange1[0], valueRange1[1]);
  values[1] = map(angle2, angleRange2[0], angleRange2[1], valueRange2[0], valueRange2[1]);
  values[2] = constrain(map(angle3-90-angle2, angleRange3[0], angleRange3[1], valueRange3[0], valueRange3[1]), 0, 180);
  values[3] = map(angle4, angleRange4[0], angleRange4[1], valueRange4[0], valueRange4[1]);
  
  //apply servo values
  Servo1.write(values[0]);
  Servo2.write(values[1]);
  Servo3.write(values[2]);
  Servo4.write(values[3]);
}

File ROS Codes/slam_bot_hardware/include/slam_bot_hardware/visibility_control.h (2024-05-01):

#ifndef SLAM_BOT_HARDWARE__VISIBILITY_CONTROL_H_
#define SLAM_BOT_HARDWARE__VISIBILITY_CONTROL_H_

// This logic was borrowed (then namespaced) from the examples on the gcc wiki:
//     https://gcc.gnu.org/wiki/Visibility

#if defined _WIN32 || defined __CYGWIN__
  #ifdef __GNUC__
    #define SLAM_BOT_HARDWARE_EXPORT __attribute__ ((dllexport))
    #define SLAM_BOT_HARDWARE_IMPORT __attribute__ ((dllimport))
  #else
    #define SLAM_BOT_HARDWARE_EXPORT __declspec(dllexport)
    #define SLAM_BOT_HARDWARE_IMPORT __declspec(dllimport)
  #endif
  #ifdef SLAM_BOT_HARDWARE_BUILDING_LIBRARY
    #define SLAM_BOT_HARDWARE_PUBLIC SLAM_BOT_HARDWARE_EXPORT
  #else
    #define SLAM_BOT_HARDWARE_PUBLIC SLAM_BOT_HARDWARE_IMPORT
  #endif
  #define SLAM_BOT_HARDWARE_PUBLIC_TYPE SLAM_BOT_HARDWARE_PUBLIC
  #define SLAM_BOT_HARDWARE_LOCAL
#else
  #define SLAM_BOT_HARDWARE_EXPORT __attribute__ ((visibility("default")))
  #define SLAM_BOT_HARDWARE_IMPORT
  #if __GNUC__ >= 4
    #define SLAM_BOT_HARDWARE_PUBLIC __attribute__ ((visibility("default")))
    #define SLAM_BOT_HARDWARE_LOCAL  __attribute__ ((visibility("hidden")))
  #else
    #define SLAM_BOT_HARDWARE_PUBLIC
    #define SLAM_BOT_HARDWARE_LOCAL
  #endif
  #define SLAM_BOT_HARDWARE_PUBLIC_TYPE
#endif

#endif  // SLAM_BOT_HARDWARE__VISIBILITY_CONTROL_H_

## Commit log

2024-01-17 Upload CAD files
    [Drive.step, Motor.step]
2024-01-17 Add motor & encoder testing codes
2024-01-18 Make PID controller for motor speed.
2024-01-22 Implemented Arduino serial control for the velocity
    [pyvenv.cfg]
2024-01-22 Implemented 2-way (almost) communication for commands and velocity feedback
2024-01-23 Finalize 2-way comms between Arduino and Jetson Nano (now fully working), and completing the Arduino Serial ROS Node that publishes odometry and receives velocity commands
2024-01-25 Correct arduino serial node odometry calculations, made robot URDF description, launch files for the robot state publisher, joint publisher, rviz to visualize it, the slam node and the navigation one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
    [slam_bot_description.urdf]
2024-01-26 Add media, circuit/connections, and edit README.md
    [slam_bot.fzz]
2024-01-26 Update .gitignore and SLAM Navigation RViz & Camera Compressed.mp4
2024-04-29 Design & make camera mount & robotic arm (with parallel linkages), wire & control servos using Arduino, change Arduino comms code to integrate sensor values, but not working since it needs ROS 2 Cont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
    [ArmMountCase.stl, Bridge.stl, CameraMountFront.stl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]
2024-05-01 Create ROS2 package with the ROS2 Control hardware component (to be implemented), add the python class (inside the respective package) with the functions for communicating with the Arduino, fix the c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
    [ROSSerial.ino, visibility_control.h]
2024-05-01 Modify code to reflect servo angle constraints in the angles sent back from the Arduino (now sends real angles not just copied ones)
